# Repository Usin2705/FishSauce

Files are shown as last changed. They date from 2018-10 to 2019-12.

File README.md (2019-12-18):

# Wall-F
<b>IoT project 2018</b>  
Metropolia UAS, 2018.  
Team members: Nhan Tran, JingXuan Wu, Nhan Phan.  

<b>Intro video</b>  
   
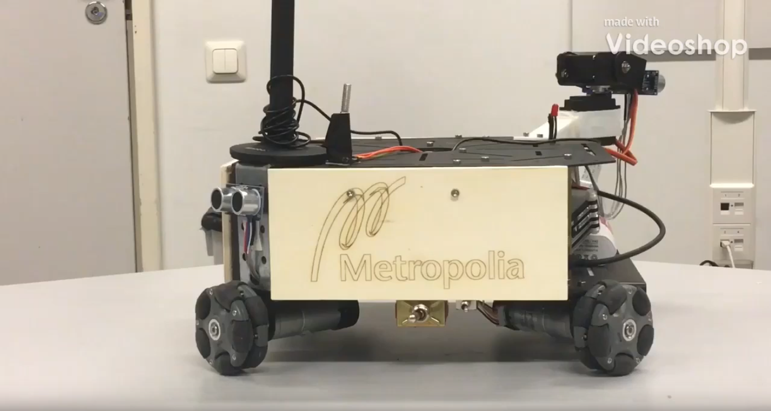
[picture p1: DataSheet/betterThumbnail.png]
Watch the video (https://youtu.be/Oxn9pmZXiwQ)
  

Hardware:  
Raspberry Pi3 B+ (with RPi camera module, microphone, mini speaker). Powered by power bank.  
LPC1549 LPCXpresso board (with 2 Ultrasonic Sensors, 2 Servo Motors, 2 L298N Motor Drivers, 1 HC-12 Wireless Serial Port Communication Module, 1 LED). Powered by power bank.  

4 Omni Wheels with 4 9V DC motors (with Hall Sensor), steel frames, wood frames with laser engraved (from another Metropolia school project), switches, 3D printed mount, steel hinge. Powered by 8 1.2V, 2800mAh Ni-MH batteries.  

Funduino Joystick Shield (not showed in the video) with HC-12 Wireless Serial Port Communication Module. Powered by 9V battery.  

3 ESP32 LOLIN D32 Pro V2.0.0 (not showed in the video). Intended to be used as BLE beacons for indoor positioning, but not managed to including it in the end of the course (worked but need a lot of improvements).  

<b>Voice recognition</b>  

Watch the video (https://youtu.be/FwI58awtriI)  

RPi captures the voice command via microphone, save it as a "wav" file. The file then uploaded to Google Cloud, using Google Cloud Speech-to-Text to translate the voice to text strings. RPi receives the text strings from Google Cloud and processing the text string to identify the correct command. RPi reply using mini speakek, and send command to LPC1549 via Uart.  

Because the time to upload the "wav" file and then received the text string back is long (due to internet speed and Google's processing speed), we used 1 LED to indicate the robot is "thinking".  

Note: due to Google Cloud Speech-to-Text is a paid service (only free for 1,000 requests/month), a mini switch is used to toogle on/off this Voice recognition module. 

In the video you can see that Wall-F recognizes the voice command from our team member and reply back.  

<b>Voice command</b>  

Watch the video (https://youtu.be/IM_iczHviLY)  

In this video Wall-F move according to the command from user.  

We add some improvement for the speech recognition module. We hard code synonyms ("turn", "rotate") so the car can understand our intention easier. Because our English is not as good as native speak,We also added some adjustment to the module as well (Our "turn", "done" is very similar).  

In the video, you can see our team member holding a wooden board. That is to demostrate our ultrasonic sensors. We have 1 in the front, right beside the camera, and 1 in the back. If the ultrasonic sensors detect obstacle in front or back, it will block the car movement in that direction. However, you still see it can hit the wall if the angle is too low (as the waves take longer time to travel back). This is the common limitation of ultrasonic sensors. You can either add more ultrasonics sensors to the cars, or idealy buy or make a 360° ultrasonic sensors, if you want to solve this problem.  

We can also use LiDAR sensor to improve it 360° long range detection. Howver, LiDAR can't detect objects in short range so we still need to rely on Ultrasonic sensors.  

<b>Face Recognition</b>  

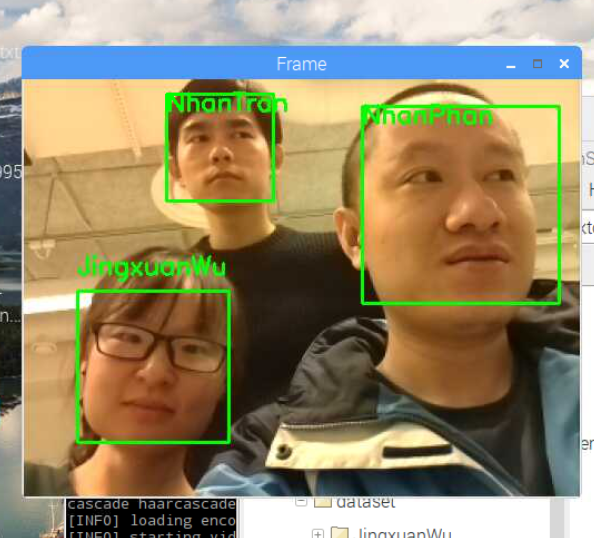
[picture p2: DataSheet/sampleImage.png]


We trained our Wall-F using our team member's face and our instructor's face, so it can recognize 4 different face together. If it see a familiar face Wall-F will speak out loud his/her name.  

The Face Recognition have two steps. The first step is "Face Detection" using Haar Feature-based Cascade Classifiers. After detect all face available in the picture, in step 2, it will pass all faces image to our trained data. If the face image is similar to what we have trained it, it will "recognize" the face and output the result. Otherwise the face will be labeled as "Unknown". The key point here is to edit the "tolerance" level, high tolerance will make the model wrongly recognize unknown face as our faces, while low tolerance make it more difficult to recognized a trained face.  
   
Watch the video (https://youtu.be/Zycl3cfg9Co)  

In this video, aside from Face Recognition, you can also see Wall-F face tracking module. We programmed it so that it will track the face of one of our members (Nhan Phan), and will also move the camera so that his face is placed in the center of the picture. If it is tracking his face and Nhan moved out of the camera, it will move the camera around to look for him.  

<b>Face Following</b>  

Watch the video (https://youtu.be/7ia6n6tgUho)  

Wall-F also have a different mode called "Face Following". If this mode is turn on (using voice control), it will stop all face Tracking, and move the camera upward. Upon regconized the face of our team member, it will move closer to him. Howver, in reality, the RPi camera is not good with handling ligth from lightbulbs in the celling (and we have a lot of celling lights in our school). As a result, picture took by the RPi when the camera moving up is very difficult to see, and make face recognition from those picture almost impossible.  

<b>Streaming to TV</b>  

Watch the video (https://youtu.be/W5ZhVK1BvL4)  

This video is just to demostate the ability to steam the video to any IoT devices. In this case it's our smart TV. As long as they share the same network, we can log in the video feed to see real time data from Wall-F.  

Link to the LPC1549 codes, which handle the commands sent from Raspberry Pi 3, commands from HC-12 wireless module, control the motors, camera and ultrasonic sensor: https://github.com/Usin2705/FishSauce/tree/master/LPCmotor  

Link to the Raspberry Pi3 codes, which contain several sub packages (UartCommunication: Uart communication with LPC1549, camModule: handle the face regconition, speechRegModule: handle the connection with Google Cloud Service and handle the voice control from users, ttsModule: allow Wall-F to speak using a mini speaker, and textVerifyModule: utility modules help with the voice regconition): https://github.com/Usin2705/FishSauce/tree/master/RaspberryPi3. All sub packages are then grouped together and run with multiprocessing library in Python. Heavy modules (voice regconition and face regconition) are run using bash script startVoiceCam.sh, other modules is run via startMotor.sh.  

Repository also contains other features. Some which we wanted to implement but were not finished due to time constraint. BLE indoor positioning is one of those. While we managed to make it work, its accuracy did not satisfy our requirement. And we did not have time to make adjustment (or experimenting with others BLE device) to improve it.
   
<b>Schematic</b>  

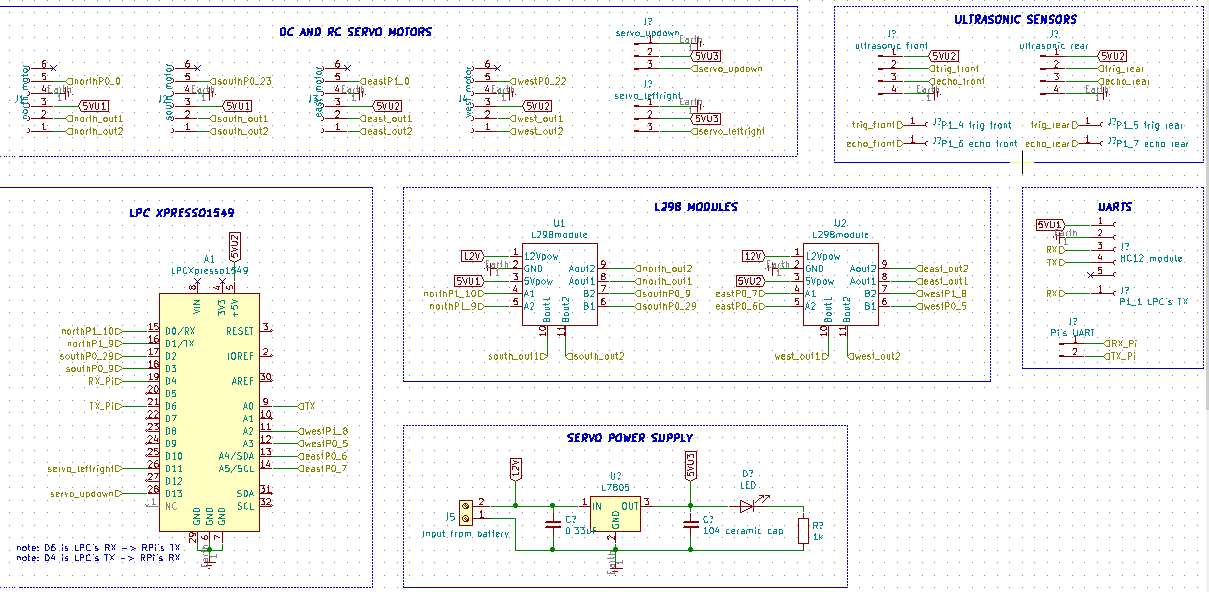
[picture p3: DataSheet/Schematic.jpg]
Schematic


Actual PCB, this was done much later after our project, as our PCB machine was broken at the time. And we do not have enough budget and time for the PCB. The PCBs here are made by https://jlcpcb.com/, and they arrived near the summer of 2019.

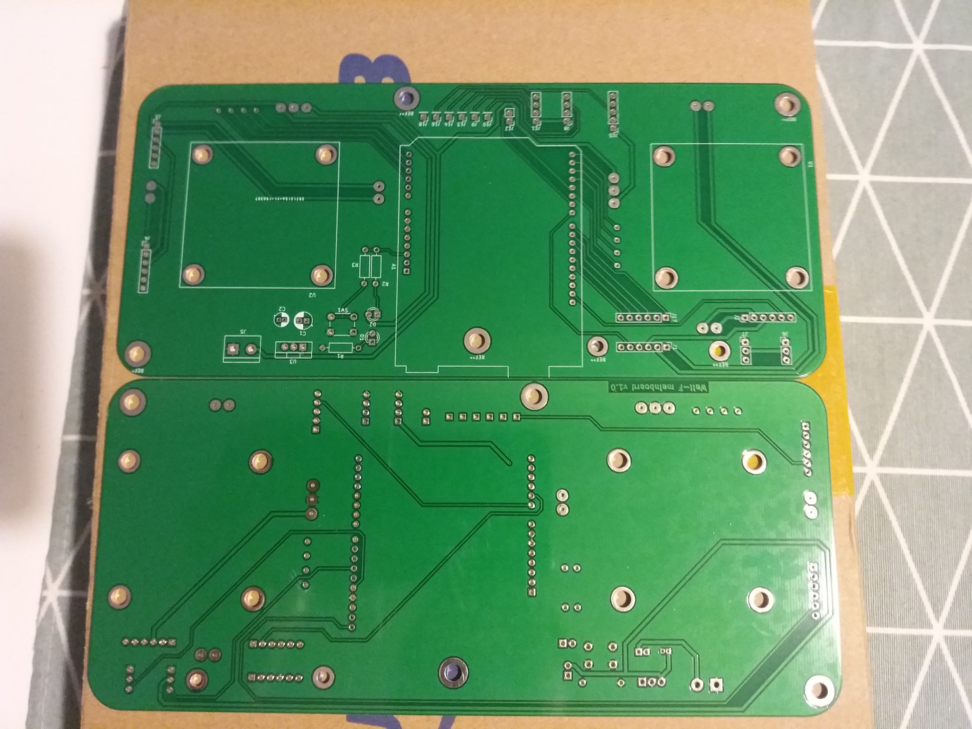
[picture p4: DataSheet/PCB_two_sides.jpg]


Excellent work from my teammate in designing the PCB. It has no big error when we connect all the cables, LEDs and Buttons. Our Wall-F look a lot nicer than before.

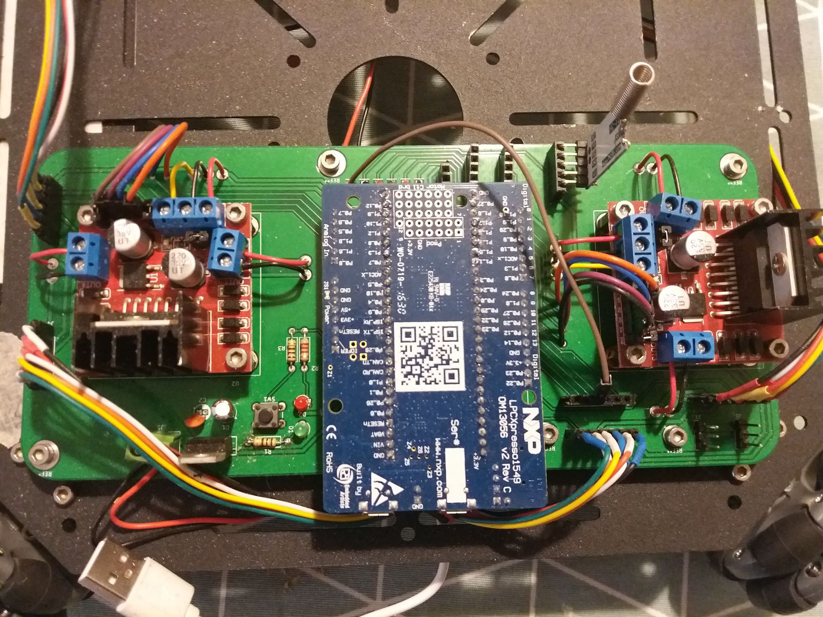
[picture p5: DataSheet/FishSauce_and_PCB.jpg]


# License

Copyright 2018

Licensed under the Apache License, Version 2.0 (the "License");
you may not use this file except in compliance with the License.
You may obtain a copy of the License at

   http://www.apache.org/licenses/LICENSE-2.0

Unless required by applicable law or agreed to in writing, software
distributed under the License is distributed on an "AS IS" BASIS,
WITHOUT WARRANTIES OR CONDITIONS OF ANY KIND, either express or implied.
See the License for the specific language governing permissions and
limitations under the License.

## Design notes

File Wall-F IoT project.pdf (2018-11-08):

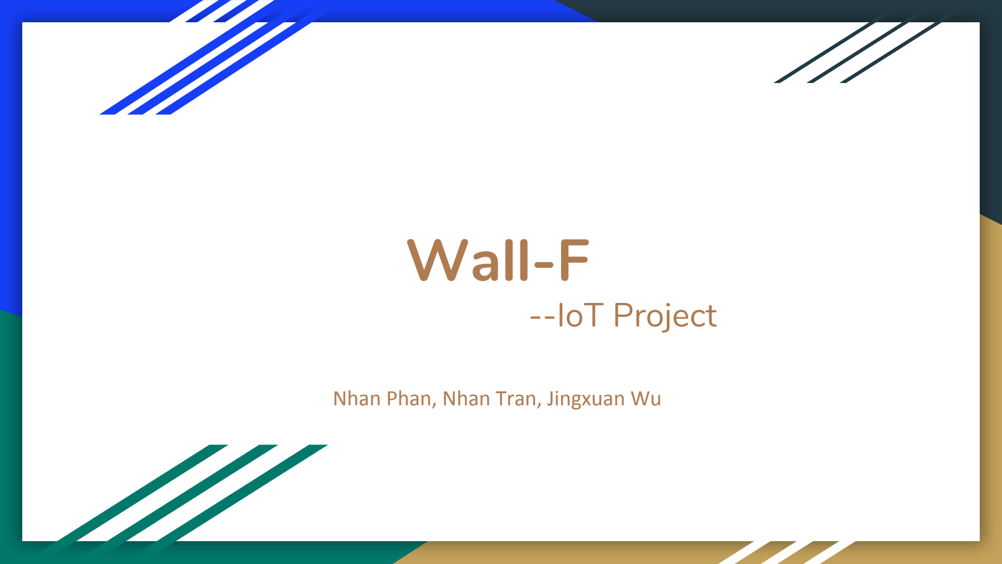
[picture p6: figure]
Wall-F; --IoT Project; Nhan Phan, Nhan Tran, Jingxuan Wu

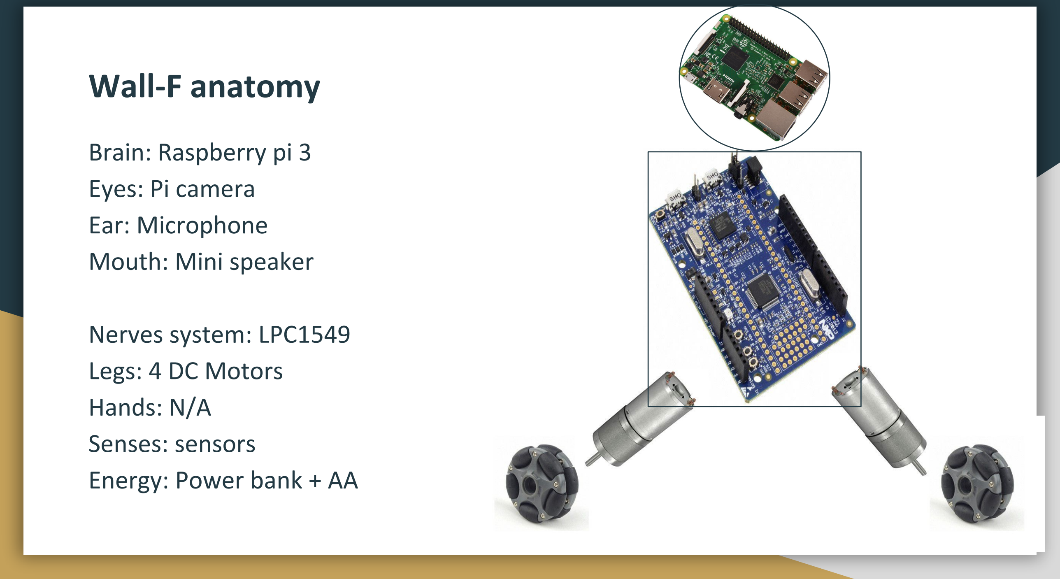
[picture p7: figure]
Wall-F anatomy; Brain: Raspberry pi 3 Eyes: Pi camera Ear: Microphone Mouth: Mini speaker; Nerves system: LPC1549 Legs: 4 DC Motors Hands: N/A Senses: sensors Energy: Power bank + AA

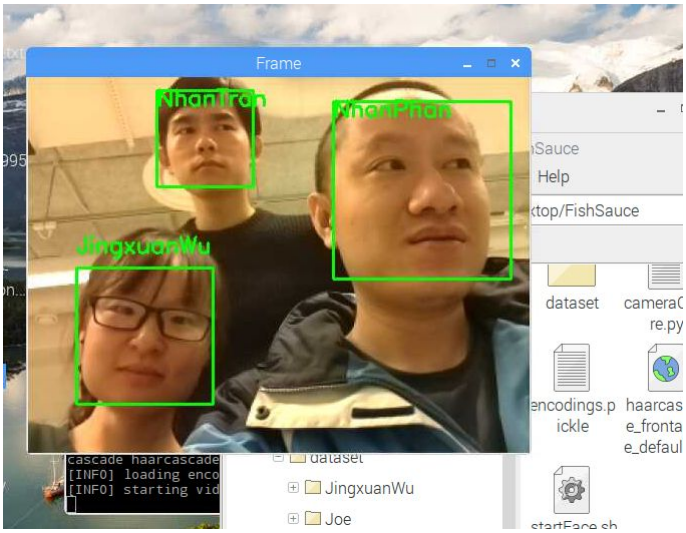
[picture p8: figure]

## Minimum goal

Facial recognition with Raspberry Pi

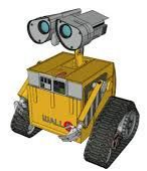
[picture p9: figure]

Voice command by Google Speech Recognition

Speaking with package “Text to Speech”

Move the robot with command

All functions work together as one system

## What else?

Using Radio frequency and Wifi to control the robot

Using Bluetooth for indoor positioning

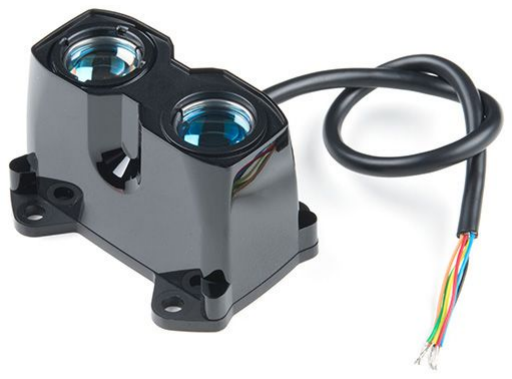
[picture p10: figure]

Carrying objects (with or without arm)

3D scanning with LiDAR sensor

Robot following object/person

Autonomous driving

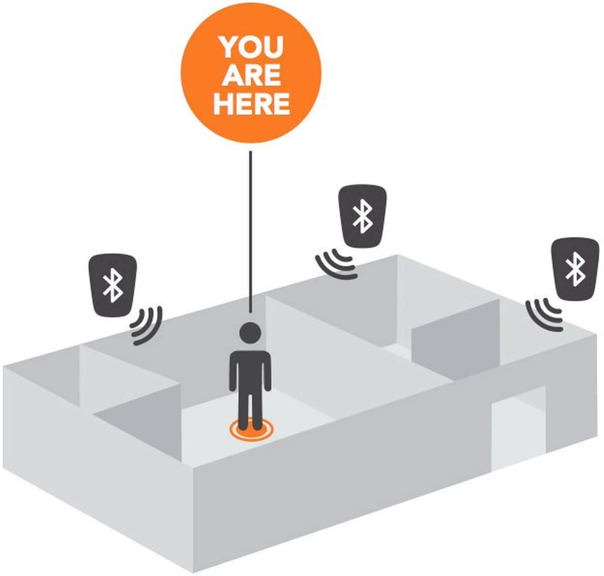
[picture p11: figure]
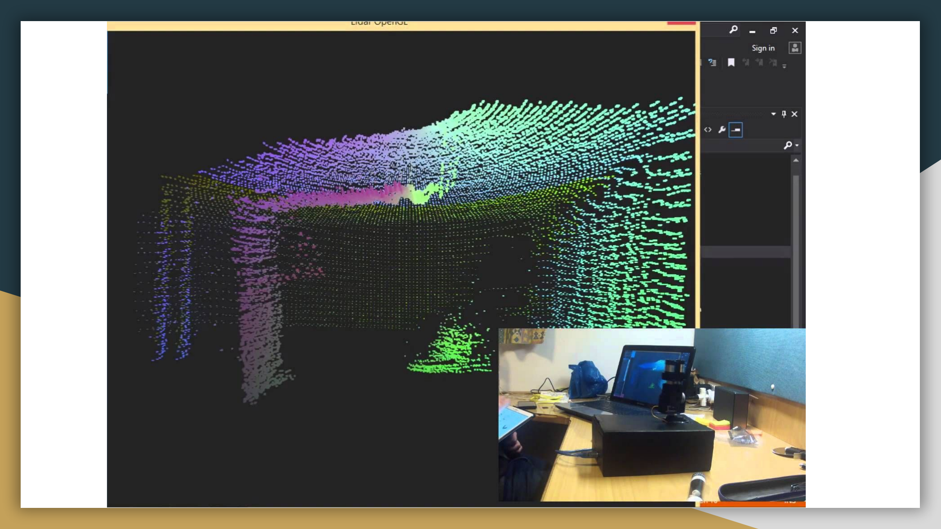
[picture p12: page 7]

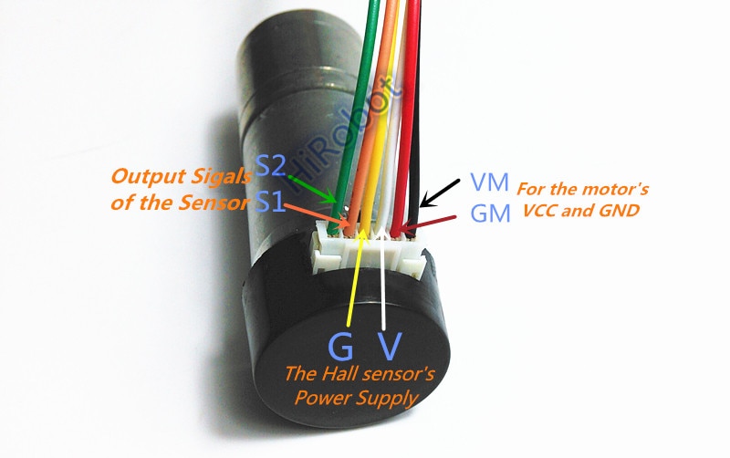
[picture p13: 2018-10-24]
DataSheet/HM-GM-25-370 gear motor.jpg

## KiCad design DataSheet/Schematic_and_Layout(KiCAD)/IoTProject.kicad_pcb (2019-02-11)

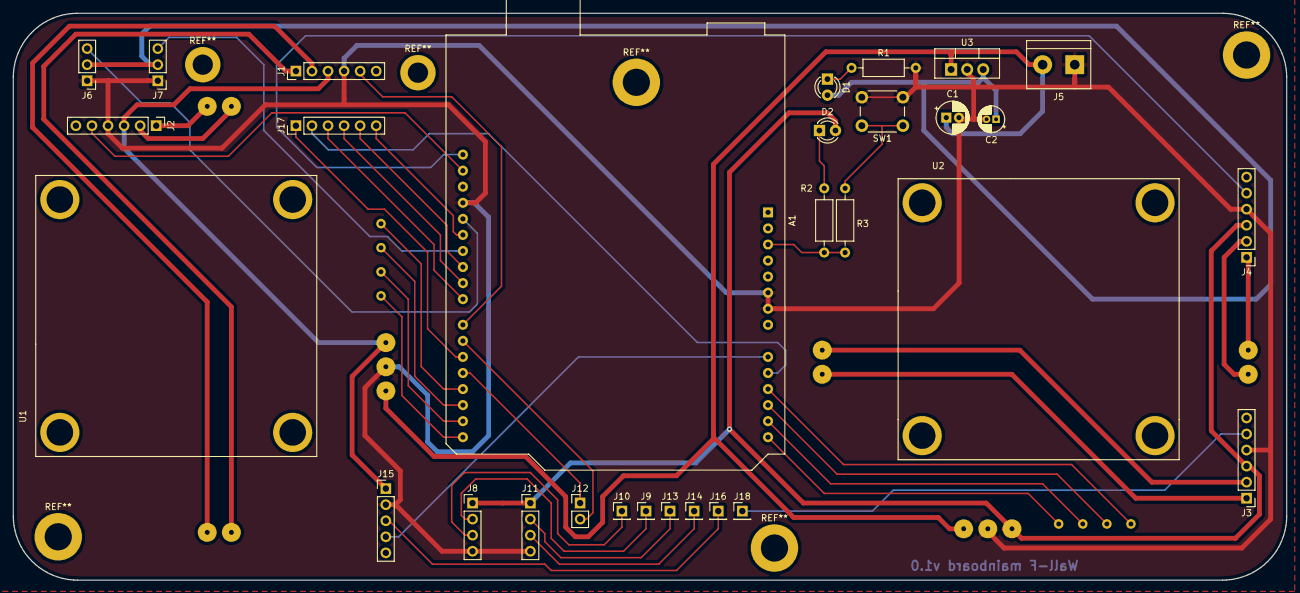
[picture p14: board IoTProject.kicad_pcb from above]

Board: 2 copper layers, 201.4 x 89.7 mm, 30 parts (0 on the bottom side), 45 nets.

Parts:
A1: LPCXpresso1549; Arduino_UNO_R3
C1: 0.33uF; CP_Radial_D5.0mm_P2.00mm
C2: 104 ceramic; CP_Radial_D4.0mm_P1.50mm
D1: 5VU3 LED; LED_D3.0mm
D2: reset LED; LED_D3.0mm
J1: north motor; PinHeader_1x06_P2.54mm_Vertical
J2: south motor; PinHeader_1x06_P2.54mm_Vertical
J3: east motor; PinHeader_1x06_P2.54mm_Vertical
J4: west motor; PinHeader_1x06_P2.54mm_Vertical
J5: 9 -12V Input; TerminalBlock_bornier-2_P5.08mm
J6: servo_updown; PinHeader_1x03_P2.54mm_Vertical
J7: servo_leftright; PinHeader_1x03_P2.54mm_Vertical
J8: ultrasonic front; PinHeader_1x04_P2.54mm_Vertical
J9: P1_4 trig fron; PinHeader_1x01_P2.54mm_Vertical
J10: P1_6 ech fron; PinHeader_1x01_P2.54mm_Vertical
J11: ultrasonic rear; PinHeader_1x04_P2.54mm_Vertical
J12: Pi's UART; PinHeader_1x02_P2.54mm_Vertical
J13: P1_5 trig rear; PinHeader_1x01_P2.54mm_Vertical
J14: P1_7 ech rear; PinHeader_1x01_P2.54mm_Vertical
J15: HC12 module; PinHeader_1x05_P2.54mm_Vertical
J16: P1_1 LPCs TX; PinHeader_1x01_P2.54mm_Vertical
J17: extender; PinHeader_1x06_P2.54mm_Vertical
J18: extenfer P1_0; PinHeader_1x01_P2.54mm_Vertical
R1: 1k; R_Axial_DIN0207_L6.3mm_D2.5mm_P10.16mm_Horizontal
R2: 2.2k; R_Axial_DIN0207_L6.3mm_D2.5mm_P10.16mm_Horizontal
R3: 100R; R_Axial_DIN0207_L6.3mm_D2.5mm_P10.16mm_Horizontal
SW1: SW_Push; SW_PUSH_6mm
U1, U2: L298module; l298module
U3: L7805; TO-220-3_Vertical

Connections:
5VU1: J1.3, J2.3, J15.1, U1.3
5VU2: D2.2, J3.3, J4.3, J8.1, J11.1, U2.3
5VU3: C2.1, D1.2, J6.2, J7.2, U3.3
12V: C1.1, J5.2, U1.1, U2.1, U3.1
A1: A1.10, J17.2
Earth: A1.6, A1.7, A1.29, C1.2, C2.2, J1.4, J2.4, J3.4, J4.4, J5.1, J6.1, J7.1, J8.4, J11.4, J15.2, R1.2, SW1.2, U1.2, U2.2, U3.2
unnamed: A1.3, R2.2, R3.2
unnamed: A1.20, J17.1
unnamed: A1.23, J17.3
unnamed: A1.24, J17.4
unnamed: A1.25, J17.5
unnamed: A1.27, J17.6
unnamed: D1.1, R1.1
unnamed: D2.1, R2.1
unnamed: R3.1, SW1.1
RX: J15.3, J16.1
RX_Pi: A1.19, J12.1
TX: A1.9, J15.4
TX_Pi: A1.21, J12.2
eastP0_6: A1.13, U2.5
eastP0_7: A1.14, U2.4
eastP1_0: J3.5, J18.1
east_out1: J3.2, U2.8
east_out2: J3.1, U2.9
echo_front: J8.3, J10.1
echo_rear: J11.3, J14.1
northP0_0: A1.22, J1.5
northP1_9: A1.16, U1.5
northP1_10: A1.15, U1.4
north_out1: J1.2, U1.8
north_out2: J1.1, U1.9
servo_leftright: A1.26, J7.3
servo_updown: A1.28, J6.3
southP0_9: A1.18, U1.7
southP0_23: A1.31, J2.5
southP0_29: A1.17, U1.6
south_out1: J2.2, U1.10
south_out2: J2.1, U1.11
trig_front: J8.2, J9.1
trig_rear: J11.2, J13.1
westP0_5: A1.12, U2.6
westP0_22: A1.32, J4.5
westP1_8: A1.11, U2.7
west_out1: J4.2, U2.10
west_out2: J4.1, U2.11

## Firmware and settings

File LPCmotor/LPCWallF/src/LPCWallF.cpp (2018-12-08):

/*
===============================================================================
 Name        : main.c
 Author      : $(author)
 Version     :
 Copyright   : $(copyright)
 Description : main definition
===============================================================================
 */
#include <cr_section_macros.h>

#include "FreeRTOS.h"
#include "task.h"
#include <cstring>
#include "DigitalIoPin.h"
#include "OmniCar.h"
#include "Command.h"
#include "queue.h"
#include "ITM_write.h"
#include "string"
#include "RPSerial.h"
#include "HCSerial.h"

// TODO: global variables here
#define CAM_X_CENTER 1500
#define CAM_X_LEFT 2350
#define CAM_X_RIGHT 700

#define CAM_Y_CENTER 2380
#define CAM_Y_UP 1100

// Queue for gcode command structs
QueueHandle_t cmdQueue;
volatile uint32_t pulse_north = 0;
volatile uint32_t pulse_south = 0;
volatile uint32_t pulse_east = 0;
volatile uint32_t pulse_west = 0;
OmniCar omniCar;

// TODO: definitions and declarations here
static void vTaskReceiveRP(void *pvParameters);
static void vTaskReceiveHC(void *pvParameters);
static void vTaskMotor(void *pvParameters);
void carindimove(OmniCar &omnicar, WHEEL wheel, bool dir, uint32_t pulse);
void SCT1_SERVO_Init();
void SCT0_TIMER_Init();
int cameraMoveX(int pos);
int cameraMoveY(int pos);
DIRECTION carDirection;
double LIMIT_DISTANCE = 15.0;  //measured in cm
volatile double ARRAYFRONT[3] = {0,0,0};
volatile double ARRAYBACK[3] = {0,0,0};

int main(void) {
	cmdQueue = xQueueCreate(5, sizeof(Command));
	SCT1_SERVO_Init();
	SCT0_TIMER_Init();
	xTaskCreate(vTaskReceiveRP, "receiveRP",
			configMINIMAL_STACK_SIZE + 350, NULL, (tskIDLE_PRIORITY + 1UL),
			(TaskHandle_t *) NULL);

	xTaskCreate(vTaskReceiveHC, "receiveHC",
			configMINIMAL_STACK_SIZE + 350, NULL, (tskIDLE_PRIORITY + 1UL),
			(TaskHandle_t *) NULL);

	xTaskCreate(vTaskMotor, "motor",
			configMINIMAL_STACK_SIZE + 100, NULL, (tskIDLE_PRIORITY + 1UL),
			(TaskHandle_t *) NULL);


	vTaskStartScheduler();

	return 1;
}

static void vTaskReceiveRP(void *pvParameters) {
	int c = 0;
	std::string str = "";
	Command cmd;
	RPSerial rpSerial;
	while(1){
		c = rpSerial.read();
		if(c != EOF){
			if (c!= '\r') {
				Board_UARTPutChar(c);
				str += (char) c;
			} else {
				Board_UARTPutSTR("\r\n");
				sscanf(str.c_str(),"%s %d",cmd.cmd_type,&cmd.count);
				if(xQueueSendToBack(cmdQueue, &cmd, portMAX_DELAY) == pdPASS){
				} else {

				}

				str = "";
			}
		}
	}
}

static void vTaskReceiveHC(void *pvParameters) {
	int c = 0;
	std::string str = "";
	Command cmd;
	HCSerial hcSerial;
	hcSerial.write("AT+C001", strlen("AT+C001"));
	while(1){
		c = hcSerial.read();
		if(c != EOF){
			if (c!= '\r') {
				Board_UARTPutChar(c);
				str += (char) c;
			} else {
				Board_UARTPutSTR("\r\n");
				sscanf(str.c_str(),"%s %d",cmd.cmd_type,&cmd.count);
				if(xQueueSendToBack(cmdQueue, &cmd, portMAX_DELAY) == pdPASS){
				} else {

				}

				str = "";
			}
		}
	}
}

static void vTaskMotor(void *pvParameters) {

	Command cmd;
	int xPos = CAM_X_CENTER;
	int yPos = CAM_Y_CENTER;
	DigitalIoPin trig(1, 4, DigitalIoPin::output, false);
	DigitalIoPin trig2(1, 5, DigitalIoPin::output, false);

	while(1){
		if(xQueueReceive(cmdQueue, (void*) &cmd, 0)) {
			if (strcmp(cmd.cmd_type, "left") == 0) {
				xPos = cameraMoveX(CAM_X_LEFT);
				yPos = cameraMoveY(CAM_Y_CENTER);
				carDirection = LEFT;
				trig.write(true);
				vTaskDelay(65);
				trig.write(false);
				carindimove(omniCar, NORTH, CLOCKWISE, cmd.count);
				carindimove(omniCar, SOUTH, COUNTERCLOCKWISE, cmd.count);
			} else if (strcmp(cmd.cmd_type, "right") == 0)  {
				xPos = cameraMoveX(CAM_X_RIGHT);
				yPos = cameraMoveY(CAM_Y_CENTER);
				carDirection = RIGHT;
				trig.write(true);
				vTaskDelay(65);
				trig.write(false);
				carindimove(omniCar, NORTH, COUNTERCLOCKWISE, cmd.count);
				carindimove(omniCar, SOUTH, CLOCKWISE, cmd.count);
			} else if (strcmp(cmd.cmd_type, "up") == 0)  {
				xPos = cameraMoveX(CAM_X_CENTER);
				yPos = cameraMoveY(CAM_Y_CENTER);
				carDirection = UP;
				trig.write(true);
				vTaskDelay(65);
				trig.write(false);
				carindimove(omniCar, EAST, CLOCKWISE, cmd.count);
				carindimove(omniCar, WEST, COUNTERCLOCKWISE, cmd.count);
			} else if (strcmp(cmd.cmd_type, "down") == 0)  {
				carDirection = DOWN;
				trig2.write(true);
				vTaskDelay(65);
				trig2.write(false);
				carindimove(omniCar, EAST, COUNTERCLOCKWISE, cmd.count);
				carindimove(omniCar, WEST, CLOCKWISE, cmd.count);
			} else if (strcmp(cmd.cmd_type, "turnl") == 0)  {
				carindimove(omniCar, NORTH, CLOCKWISE, cmd.count);
				carindimove(omniCar, SOUTH, CLOCKWISE, cmd.count);
				carindimove(omniCar, EAST, CLOCKWISE, cmd.count);
				carindimove(omniCar, WEST, CLOCKWISE, cmd.count);
			} else if (strcmp(cmd.cmd_type, "turnr") == 0){
				carindimove(omniCar, NORTH, COUNTERCLOCKWISE, cmd.count);
				carindimove(omniCar, SOUTH, COUNTERCLOCKWISE, cmd.count);
				carindimove(omniCar, EAST, COUNTERCLOCKWISE, cmd.count);
				carindimove(omniCar, WEST, COUNTERCLOCKWISE, cmd.count);
			} else if (strcmp(cmd.cmd_type, "caml") == 0){
				xPos = cameraMoveX(xPos + cmd.count);
			} else if (strcmp(cmd.cmd_type, "camr") == 0){
				xPos = cameraMoveX(xPos - cmd.count);
			} else if (strcmp(cmd.cmd_type, "camu") == 0){
				yPos = cameraMoveY(yPos - cmd.count);
			} else if (strcmp(cmd.cmd_type, "camd") == 0){
				yPos = cameraMoveY(yPos + cmd.count);
			} else if (strcmp(cmd.cmd_type, "camm") == 0){
				xPos = cameraMoveX(CAM_X_CENTER);
			} else if (strcmp(cmd.cmd_type, "camf") == 0){
				xPos = cameraMoveX(CAM_X_CENTER);
				yPos = cameraMoveY(2100);
			} else if (strcmp(cmd.cmd_type, "camc") == 0){
				xPos = cameraMoveX(CAM_X_CENTER);
				yPos = cameraMoveY(CAM_Y_CENTER);
			}
		}
	}
}

void carindimove(OmniCar &omnicar, WHEEL wheel, bool dir, uint32_t pulse) {
	switch(wheel) {
	case NORTH:
		pulse_north = pulse;
		break;
	case SOUTH:
		pulse_south = pulse;
		break;
	case EAST:
		pulse_east = pulse;
		break;
	case WEST:
		pulse_west = pulse;
		break;
	}
	omnicar.indiMove(wheel, dir);
}

void SCT1_SERVO_Init(){
	Chip_SCT_Init(LPC_SCTLARGE1);

	Chip_SWM_MovablePortPinAssign(SWM_SCT1_OUT0_O, 0,28); //Servox
	Chip_SWM_MovablePortPinAssign(SWM_SCT1_OUT1_O, 0,14); //Servoy

	LPC_SCTLARGE1->CONFIG |= (1 << 17); // two 16-bit timers, auto limit

	LPC_SCTLARGE1->CTRL_L |= (72-1) << 5; // set prescaler, SCTimer/PWM clock = 1 MHz

	LPC_SCTLARGE1->MATCHREL[0].L = 20000; // match 0 @ 10/1MHz = 10 usec (100 kHz PWM freq) (1MHz/20000)
	LPC_SCTLARGE1->MATCHREL[1].L = CAM_X_CENTER; // match 1 used for duty cycle (in 10 steps)
	LPC_SCTLARGE1->MATCHREL[2].L = CAM_Y_CENTER; // match 1 used for duty cycle (in 10 steps)
	LPC_SCTLARGE1->EVENT[0].STATE = 0xFFFFFFFF; // event 0 happens in all states
	LPC_SCTLARGE1->EVENT[0].CTRL = (1 << 12); // match 0 condition only
	LPC_SCTLARGE1->EVENT[1].STATE = 0xFFFFFFFF; // event 1 happens in all states
	LPC_SCTLARGE1->EVENT[1].CTRL = (1 << 0) | (1 << 12); // match 1 condition only
	LPC_SCTLARGE1->EVENT[2].STATE = 0xFFFFFFFF; // event 2 happens in all states
	LPC_SCTLARGE1->EVENT[2].CTRL = (2 << 0) | (1 << 12); // match 2 condition only

	LPC_SCTLARGE1->OUT[0].SET = (1 << 0); // event 0 will set SCTx_OUT0
	LPC_SCTLARGE1->OUT[0].CLR = (1 << 1); // event 1 will clear SCTx_OUT0

	LPC_SCTLARGE1->OUT[1].SET = (1 << 0); // event 0 will set SCTx_OUT1
	LPC_SCTLARGE1->OUT[1].CLR = (1 << 2); // event 2 will clear SCTx_OUT1

	LPC_SCTLARGE1->CTRL_L &= ~(1 << 2); // unhalt it by clearing bit 2 of CTRL reg
}

void SCT0_TIMER_Init()
{
	Chip_INMUX_SelectSCT0Src(0, SCT0_INMUX_PIO1_6);			// SCT2_IN0 at P1_6
	Chip_INMUX_SelectSCT0Src(1, SCT0_INMUX_PIO1_7);			// SCT2_IN0 at P1_7

	LPC_SYSCON->SYSAHBCLKCTRL[1] |= (1 << 2);                			// enable the SCT0 clock
	LPC_SCT0->CONFIG           |= (1 << 0);			      			// unified

	LPC_SCT0->CTRL_U        |= (72 << 5);       					// set pre-scaler, system clock is 72MHz

	LPC_SCT0->REGMODE_L      = (1 << 0) | (1 << 1)
																											 | (1 << 2) | (1 << 3);        			// CAP 0 and CAP 1


	LPC_SCT0->EVENT[1].STATE = 0xFFFFFFFF;                 			// event 1 happens in all states
	LPC_SCT0->EVENT[1].CTRL  = (1 << 10) | (2 << 12);      			// IN_0 rising edge condition only

	LPC_SCT0->EVENT[2].STATE = 0xFFFFFFFF;                 			// event 2 happens in all states
	LPC_SCT0->EVENT[2].CTRL  = (2 << 10) | (2 << 12);      			// IN_0 falling edge condition only

	LPC_SCT0->EVENT[3].STATE = 0xFFFFFFFF;                 			// event 3 happens in all states
	LPC_SCT0->EVENT[3].CTRL  = (1 << 10) | (2 << 12) | (1 << 6);    // IN_1 rising edge condition only

	LPC_SCT0->EVENT[4].STATE = 0xFFFFFFFF;                 			// event 4 happens in all states
	LPC_SCT0->EVENT[4].CTRL  = (2 << 10) | (2 << 12) | (1 << 6);    // IN_1 falling edge condition only

	LPC_SCT0->CAPCTRL[0].U   = (1 << 1);                   			// event 1 is causing capture 0
	LPC_SCT0->CAPCTRL[1].U   = (1 << 2);       			   			// event 2 cause capture 1
	LPC_SCT0->CAPCTRL[2].U   = (1 << 3);                   			// event 3 is causing capture 2
	LPC_SCT0->CAPCTRL[3].U   = (1 << 4);       			   			// event 4 cause capture 3

	LPC_SCT0->OUT[0].SET     = (1 << 1);                   			// event 1 set   OUT0 LED ON
	LPC_SCT0->OUT[0].CLR     = (1 << 2);                   			// event 2 clear OUT0 LED OFF

	LPC_SCT0->EVEN           = (1 << 2) | (1 << 4);        		   			// event 2 generate an irq

	NVIC_EnableIRQ(SCT0_IRQn);                             			// enable SCT0 interrupt

	LPC_SCT0->CTRL_U           &= ~(1 << 2);               			// start timer
}

/*	Move the X Servo
 * 	2450: full left
 * 	750: full right
 * 	1500 middle
 *
 */
int cameraMoveX(int pos){
	if (pos>CAM_X_LEFT) pos = CAM_X_LEFT;
	if (pos<CAM_X_RIGHT) pos = CAM_X_RIGHT;
	LPC_SCTLARGE1->MATCHREL[1].L = pos;
	return pos;
}


/*	Move the Y Servo
 * 	2380: front
 * 	1500: top
 * 	1100: back
 *
 */
int cameraMoveY(int pos){
	if (pos > CAM_Y_CENTER) pos = CAM_Y_CENTER;
	if (pos < CAM_Y_UP) pos = CAM_Y_UP;
	LPC_SCTLARGE1->MATCHREL[2].L = pos;
	return pos;
}

extern "C" {

void PIN_INT0_IRQHandler(void)			//north
{
	Chip_PININT_ClearIntStatus(LPC_GPIO_PIN_INT, PININTCH(0));
	if(pulse_north > 0) {
		pulse_north--;
	}
	else omniCar.stopWheel(NORTH);
}
void PIN_INT1_IRQHandler(void)			//south
{
	Chip_PININT_ClearIntStatus(LPC_GPIO_PIN_INT, PININTCH(1));
	if(pulse_south > 0) {
		pulse_south--;

	}
	else omniCar.stopWheel(SOUTH);
}
void PIN_INT2_IRQHandler(void)			//east
{
	Chip_PININT_ClearIntStatus(LPC_GPIO_PIN_INT, PININTCH(2));
	if(pulse_east > 0) {
		pulse_east--;
	}
	else omniCar.stopWheel(EAST);
}
void PIN_INT3_IRQHandler(void)			//west
{
	Chip_PININT_ClearIntStatus(LPC_GPIO_PIN_INT, PININTCH(3));
	if(pulse_west > 0) {
		pulse_west--;
	}
	else omniCar.stopWheel(WEST);
}

void vConfigureTimerForRunTimeStats( void ) {
	Chip_SCT_Init(LPC_SCTSMALL1);
	LPC_SCTSMALL1->CONFIG = SCT_CONFIG_32BIT_COUNTER;
	LPC_SCTSMALL1->CTRL_U = SCT_CTRL_PRE_L(255) | SCT_CTRL_CLRCTR_L; // set prescaler to 256 (255 + 1), and start timer
}

volatile double smallestOfThree(volatile double ARRAY[2]) {
	if (ARRAY[2] < ARRAY[1]) {
		return ARRAY[2]<ARRAY[0]?ARRAY[2]:ARRAY[0];
	} else {
		return ARRAY[1]<ARRAY[0]?ARRAY[1]:ARRAY[0];
	}
}

void SCT0_IRQHandler(void)
{
	uint32_t status = LPC_SCT0->EVFLAG;
	uint32_t time = 0;
	uint32_t time2 = 0;
	double distanceFront = 0;
	double distanceBack = 0;
	if(status & (1 << 2)) {
		if(LPC_SCT0->CAP[1].U >= LPC_SCT0->CAP[0].U) {
			time = LPC_SCT0->CAP[1].U - LPC_SCT0->CAP[0].U;
		}
		else {															//The counter has been reset
			time = 4294967295 - LPC_SCT0->CAP[0].U + LPC_SCT0->CAP[1].U;
		}
		distanceFront = (double)time*17.0/1000.0;
		ARRAYFRONT[2] = ARRAYFRONT[1];
		ARRAYFRONT[1] = ARRAYFRONT[0];
		ARRAYFRONT[0] = distanceFront;
		if (smallestOfThree(ARRAYFRONT) <=LIMIT_DISTANCE && (carDirection == UP)) {
			pulse_east = 0;
			pulse_west = 0;
			omniCar.stopWheel(EAST);
			omniCar.stopWheel(WEST);
			double a = 0;
		} else if ((smallestOfThree(ARRAYFRONT)<=(LIMIT_DISTANCE+15.0)) && (carDirection == LEFT || carDirection == RIGHT)) {
			pulse_north = 0;
			pulse_south = 0;
			omniCar.stopWheel(NORTH);
			omniCar.stopWheel(SOUTH);
			double a = 0;
		}
	}
	if(status & (1 << 4)) {
		if(LPC_SCT0->CAP[3].U >= LPC_SCT0->CAP[2].U) {
			time2 = LPC_SCT0->CAP[3].U - LPC_SCT0->CAP[2].U;
		}
		else {															//The counter has been reset
			time2 = 4294967295 - LPC_SCT0->CAP[2].U + LPC_SCT0->CAP[3].U;
		}
		distanceBack = (double)time2*17.0/1000.0;
		ARRAYBACK[2] = ARRAYBACK[1];
		ARRAYBACK[1] = ARRAYBACK[0];
		ARRAYBACK[0] = distanceBack;
		if (smallestOfThree(ARRAYBACK) <=LIMIT_DISTANCE && carDirection == DOWN) {
			pulse_east = 0;
			pulse_west = 0;
			omniCar.stopWheel(EAST);
			omniCar.stopWheel(WEST);
		}
	}

	LPC_SCT0->EVFLAG = status;                         				// clear interrupt

}

}

/* available pins
 	DigitalIoPin northPin1(1,10,DigitalIoPin::output,true);
	DigitalIoPin northPin2(1,9,DigitalIoPin::output,true);
	DigitalIoPin southPin1(0,29,DigitalIoPin::output,true);
	DigitalIoPin southPin2(0,9,DigitalIoPin::output,true);
	DigitalIoPin eastPin1(0,7,DigitalIoPin::output,true);
	DigitalIoPin eastPin2(0,6,DigitalIoPin::output,true);
	DigitalIoPin westPin1(0,5,DigitalIoPin::output,true);
	DigitalIoPin westPin2(1,8,DigitalIoPin::output,true);
	DigitalIoPin intsouthpin20(0,23,DigitalIoPin::output,true);//3.2
	DigitalIoPin intwestpin21(0,22,DigitalIoPin::output,true);//3.2
	DigitalIoPin inteastpin15(1,0,DigitalIoPin::output,true);//2.5
	intnorth  0 0
	DigitalIoPin servo1(0,28,DigitalIoPin::output,true);//2.5
	DigitalIoPin servo2(0,14,DigitalIoPin::output,true);//2.5
	//UART1 RPi
	DigitalIoPin pin11(0,10,DigitalIoPin::output,true);//2.5
	DigitalIoPin pin12(1,3,DigitalIoPin::output,true);//2.5
	//UART2 Control
	DigitalIoPin pin6(0,8,DigitalIoPin::output,true);//2.5
	DigitalIoPin pin5(1,6,DigitalIoPin::output,true);//2.5
	DigitalIoPin pin13(0,0,DigitalIoPin::output,true);//2.5
DigitalIoPin pin14(0,24,DigitalIoPin::output,true);//0
DigitalIoPin pin16(0,27,DigitalIoPin::output,true);//0
DigitalIoPin pin18(0,12,DigitalIoPin::output,true);//0
 */

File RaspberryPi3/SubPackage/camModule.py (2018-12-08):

# USAGE
# python pi_face_recognition.py --cascade haarcascade_frontalface_default.xml --encodings encodings.pickle

# import the necessary packages
from imutils.video import VideoStream
from imutils.video import FPS
import face_recognition
import argparse
import imutils
import pickle
import time
import cv2
import subprocess
from SubPackage.UartCommunication import UartCommunication
from SubPackage.ttsModule import tts

def scanForNhan(stepLeft, stepRight, stepUp, isScanned, uart):
	if (stepLeft == 0) and (stepRight==0):
		uart.Send_Command_To_LPC("camc \r\n")
		count= 70*stepUp
		uart.Send_Command_To_LPC("camu " +str(count)+ " \r\n")
		time.sleep(0.1)
		stepUp+=1

		if stepUp >= 12:
			isScanned = True
			uart.Send_Command_To_LPC("camc \r\n")

	if (stepLeft <=6):
		count = 50*stepLeft
		uart.Send_Command_To_LPC("caml " +str(count)+ " \r\n")
		time.sleep(0.1)
		stepLeft+=1
	else:
		count = 50*stepRight
		uart.Send_Command_To_LPC("camr " +str(count)+ " \r\n")
		time.sleep(0.1)
		stepRight+=1

	# if finish scan and can't find my face
	if (stepRight == 12):
		stepLeft=0
		stepRight=0

	return stepLeft, stepRight, stepUp, isScanned
	
def scanFollowingNhan(isScanned, uart):
	uart.Send_Command_To_LPC("camf\r\n") #caml will move to 1500 X and 1700 Y: Center
	time.sleep(0.1)
	
def readFile():
	try:
		f = open("isFollow.txt")
		line = f.readline()		
		#print(line)
		f.close()
		return line
	except Exception as error:
		print("error reading file")
		#print(error)

def faceRegconition():
	
	# construct the argument parser and parse the arguments
	ap = argparse.ArgumentParser()
	ap.add_argument("-c", "--cascade", default = "haarcascade_frontalface_default.xml",
					help = "path to where the face cascade resides")
	ap.add_argument("-e", "--encodings", default = "encodings.pickle",
					help="path to serialized db of facial encodings")
	args = vars(ap.parse_args())

	# load the known faces and embeddings along with OpenCV's Haar
	# cascade for face detection
	print("[INFO] loading encodings + face detector...")
	data = pickle.loads(open(args["encodings"], "rb").read())
	detector = cv2.CascadeClassifier(args["cascade"])

	# initialize the video stream and allow the camera sensor to warm up
	print("[INFO] starting video stream...")
	#for USB camera
	# vs = VideoStream(src=0).start()

	#for pi camera
	vs = VideoStream(usePiCamera=True).start()
	time.sleep(2.0)

	# start the FPS counter
	fps = FPS().start()
	startTime = time.time()
	startTimeNhanTran = time.time() - 60
	startTimeJingXuan = time.time() - 60
	startTimeJoe = time.time() - 60
	stepLeft = 0
	stepRight = 0
	stepUp = 0
	isScanned = False
	isSaid = False
	#make the camera stay at 1 position at least 3 times
	countForDetect = 0
	uart = UartCommunication(9600)

	# loop over frames from the video file stream
	while True:
		isFollow = (readFile()=="True")
		countForDetect+=1
		# grab the frame from the threaded video stream and resize it
		# to 500px (to speedup processing)
		frame = vs.read()
		frame = imutils.resize(frame, width=400)

		# convert the input frame from (1) BGR to grayscale (for face
		# detection) and (2) from BGR to RGB (for face recognition)
		gray = cv2.cvtColor(frame, cv2.COLOR_BGR2GRAY)
		rgb = cv2.cvtColor(frame, cv2.COLOR_BGR2RGB)

		# detect faces in the grayscale frame
		rects = detector.detectMultiScale(gray, scaleFactor=1.1,
			minNeighbors=5, minSize=(30, 30),
			flags=cv2.CASCADE_SCALE_IMAGE)

		# OpenCV returns bounding box coordinates in (x, y, w, h) order
		# but we need them in (top, right, bottom, left) order, so we
		# need to do a bit of reordering
		boxes = [(y, x + w, y + h, x) for (x, y, w, h) in rects]

		# compute the facial embeddings for each face bounding box
		encodings = face_recognition.face_encodings(rgb, boxes)
		names = []

		# loop over the facial embeddings
		for encoding in encodings:
			# attempt to match each face in the input image to our known
			# encodings
			matches = face_recognition.compare_faces(data["encodings"],
				encoding, tolerance=0.4)
			name = "Unknown"

			# check to see if we have found a match
			if True in matches:
				# find the indexes of all matched faces then initialize a
				# dictionary to count the total number of times each face
				# was matched
				matchedIdxs = [i for (i, b) in enumerate(matches) if b]
				counts = {}

				# loop over the matched indexes and maintain a count for
				# each recognized face face
				for i in matchedIdxs:
					name = data["names"][i]
					counts[name] = counts.get(name, 0) + 1

				# determine the recognized face with the largest number
				# of votes (note: in the event of an unlikely tie Python
				# will select first entry in the dictionary)
				name = max(counts, key=counts.get)

			# update the list of names
			names.append(name)

		# loop over the recognized faces
		for ((top, right, bottom, left), name) in zip(boxes, names):
			# draw the predicted face name on the image
			cv2.rectangle(frame, (left, top), (right, bottom),
				(0, 255, 0), 2)
			y = top - 15 if top - 15 > 15 else top + 15
			xAdjust = (right + left)
			yAdjust = (top + bottom)
			cv2.putText(frame, str(right) +"," + str(left)+ name, (left, y), cv2.FONT_HERSHEY_SIMPLEX, 0.75, (0, 255, 0), 2)
			if name=="Joe":
				if(time.time()-startTimeJoe) >= 60:
					tts("Hello Joseph Hotchkiss!")
				startTimeJoe = time.time()
				
			if name=="NhanTran":
				if(time.time()-startTimeNhanTran) >= 60:
					tts("Hello Mistern Yann Tran!")
				startTimeNhanTran = time.time()
				
			if name=="JingxuanWu":
				if(time.time()-startTimeJingXuan) >= 60:
					tts("Hello Jing shwan!")
				startTimeJingXuan = time.time()
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

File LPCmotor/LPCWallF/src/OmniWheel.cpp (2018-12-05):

/*
 * OmniWheel.cpp
 *
 *  Created on: Oct 25, 2018
 *      Author: Usin
 */

#include <OmniWheel.h>

OmniWheel::OmniWheel(int portPin1, int pinPin1, int portPin2, int pinPin2, int portint, int pinint, int index):
pin1(portPin1, pinPin1, DigitalIoPin::output, true),
pin2(portPin2, pinPin2, DigitalIoPin::output, true)
{
	mIsClockwise = true;
	enable = false;
	/* Set pin back to GPIO (on some boards may have been changed to something
		   else by Board_Init()) */
	Chip_IOCON_PinMuxSet(LPC_IOCON, portint, pinint,
			(IOCON_DIGMODE_EN | IOCON_MODE_INACT) );
	/* Configure GPIO pin as input */
	Chip_GPIO_SetPinDIRInput(LPC_GPIO, portint, pinint);
	/* Configure interrupt channel for the GPIO pin in INMUX block */
	Chip_INMUX_PinIntSel(index, portint, pinint);
	/* Configure channel interrupt as edge sensitive and falling edge interrupt */
	Chip_PININT_ClearIntStatus(LPC_GPIO_PIN_INT, PININTCH(index));
	Chip_PININT_SetPinModeEdge(LPC_GPIO_PIN_INT, PININTCH(index));
	Chip_PININT_EnableIntLow(LPC_GPIO_PIN_INT, PININTCH(index));
	switch (index) {
	case 0:
		NVIC_ClearPendingIRQ(PIN_INT0_IRQn);
		NVIC_EnableIRQ(PIN_INT0_IRQn);
		NVIC_SetPriority(PIN_INT0_IRQn,4);
		break;
	case 1:
		NVIC_ClearPendingIRQ(PIN_INT1_IRQn);
		NVIC_EnableIRQ(PIN_INT1_IRQn);
		NVIC_SetPriority(PIN_INT1_IRQn,4);
		break;
	case 2:
		NVIC_ClearPendingIRQ(PIN_INT2_IRQn);
		NVIC_EnableIRQ(PIN_INT2_IRQn);
		NVIC_SetPriority(PIN_INT2_IRQn,4);
		break;
	case 3:
		NVIC_ClearPendingIRQ(PIN_INT3_IRQn);
		NVIC_EnableIRQ(PIN_INT3_IRQn);
		NVIC_SetPriority(PIN_INT3_IRQn,4);
		break;
	}
}

/*
 * Rotate the motor clockwise or counter clockwise
 * if motor is rotating clockwise, pin1 must write true
 * then pin2 must write false
 * Also update the direction of the motor, just in case we need it
 * (probably need it in counting the hall signal)
 *
 */
void OmniWheel::rotate(bool isClockwise) {
	mIsClockwise = isClockwise;
	if(this->enable) {
		pin1.write(isClockwise);
		pin2.write(!isClockwise);
	}
}

bool OmniWheel::getDirection() {return mIsClockwise;}
void OmniWheel::setEnable() {this->enable = true;}
/*
 * Stop the rotation of the wheel by set both pins
 * to false
 */
void OmniWheel::stop() {
	this->enable = false;
	pin1.write(false);
	pin2.write(false);
}

OmniWheel::~OmniWheel() {
	// TODO Auto-generated destructor stub
}

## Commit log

2018-10-24 LPC motor move
2018-10-24 feat: added code from raspberry pi for face recognition
2018-10-24 feat: motor work properly
2018-10-26 feat: add Raspberrpi commnunication (not working)
    [LPCWallF.cpp, RPSerial.cpp]
2018-10-27 modify omniwheel.cpp: add interrupt pin to wheel, setup interrupt has not been tested yet because cannot add lpc15xx/inc include path which contains pinint.h
2018-10-29 finish the interrupt stuff but this yields some conflicts with the driving principal
2018-11-05 add interrupt stopping mechanism for the wheels and change pins for south and west wheel
2018-11-07 added and tested pulse mechanism for motors
2018-11-07 added and tested pulse mechanism for the wheels, the car now can move wheels independently
2018-11-08 feat: added servo control (not finish)
2018-11-08 feat: add measurement for pi camera, might need to change the X (750 and 2450 is already the maximum)
2018-11-09 feat: added camera control + movement control (arrow keys still have some error)
    [FishSauce.py, LPCWallF.cpp, UartCommunication.py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]
2018-12-05 feat: added 2nd uart
2018-12-05 bug: fixed joystick bug
    [JoyStickShield.ino]
2018-12-05 feat: added minor changes and Ultrasonic 1.0
2018-12-05 feat: almost done (need to improve the sensor)
2018-12-08 feat: add better ultrasonic sensor
2018-12-08 feat: added smoothing for ultrasonic sensor
2018-12-24 add schematic
2018-12-25 feat: added schematic pdf file
2018-12-27 add KiCAD schematic and layout files
    [IoTProject.kicad_pcb, IoTProject.sch]
2019-01-06 add sample images
2019-01-06 add the schematic image back
2019-02-11 add gerber files
    [IoTProject-B.Cu.gbr, IoTProject-B.Mask.gbr, IoTProject-B.Paste.gbr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]
2019-12-04 feat: add PCB images discard BLE changes (why it not as good as we think it should?)
